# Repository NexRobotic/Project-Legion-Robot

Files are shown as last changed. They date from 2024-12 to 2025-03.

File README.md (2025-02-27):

# Project-Legion-Robot
 This is a 12 DOF Robot Based on RPI/Arduino/ESP32
    
This Repo Have Various Version of the Robot (Basicly All you need)

1. Arduino Without Servo Driver (This is the Simplest Version of Legion with Ardduino Nano And Nano Expansion Used Serial Monitor To Control)
2. Arduino With Servo Driver (This Version Use 16 Channel PCA Servo Driver WITH Arduino Solving pins issue, USE SDA and SCL)
3. Arduino With ESPCam  ("This Version Use Espcam and arduino to give live view and control interface, Use Rx Tx")
4. ESP32 (Since FlexiTimer2.h is not working on ESP Boards, i need to Find another way to Work on this Version any, 'IF ANY IDEA PLEASE CONTRIBUTE')
5. raspberri pi (This is The python Version, I am Using RPI 4 and Servo Driver for AI and ML Integration)

and Legion MARK 2 (this is the most advanced version of all)
watch the Youtube Video here 
Legion MARK 2 (https://www.youtube.com/watch?v=k1hns6NKTCY)

What to DO ?
1. 3d Print the Structure and Pick your Code Version
2. attach the servos to the structure (Use Servo Pin image for pin connection in media folder) (*without Servo horn)
3. Use Servo_Config Code to calibrate all the servo to 90
4. Attach all the servo horn maintaining the initial position (Use Initial position image in media folder) (*IMPORTANT)
5. Complete the Circuits and Upload/Run main code and enjoy



Note: 
Main Logic I used Was by Sunfounder Robot
panerqiang@sunfounder.com

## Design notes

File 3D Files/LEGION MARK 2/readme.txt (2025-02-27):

This is what you need to print 

legs with n20 holder X 2 (it have both left and right 1 so print this 2 pairs)
backward shoulder X 2
Forward Shoulder  X 2
femur             X 4
hinge             X 8
body top          X 1
body Bottom       X 1

USE tree support cuz its the best one

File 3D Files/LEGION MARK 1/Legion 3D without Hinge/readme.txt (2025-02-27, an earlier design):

This is what you need to print 

forward legs      X 2 
Backward legs     X 2 
backward shoulder X 2
Forward Shoulder  X 2
femur             X 4
body top          X 1
body Bottom       X 1

Note :
not using hinges will need fore filament as support and it will be slightly difficult to change the servo if needed

if you use hinges you need 16 screws (4 for each leg) to connect the hinges

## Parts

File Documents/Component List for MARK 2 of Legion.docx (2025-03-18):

# Component List for MARK 2 of Legion

Component | Quantity | Price per Unit (Rs) | Total Price (Rs)
MG99s 180 Degree Servo | 12 | 189 | 2268
Arduino Nano | 1 | 293 | 293
ESP32Cam with programmer | 1 | 1199 | 1199
UBEC SWITCH (5V 3AMP) | 1 | 496 | 496
L298N Motor driver | 1 | 284 | 284
N20 DC Geared Motor with wheels | 4 | 516 | 2064
18650 Rechargeable Cell | 3 | 295 | 885
18650 Rechargeable Cell Holder | 1 | 149 | 149
16 channel Servo driver | 1 | 540 | 540
Total Cost | | | 8178

Note: 3d part not included in the price

Additional Requirements

- On off Switch
- Jumper wires
- 3d printed parts and screws
- Antenna for esp32cam (optional)
- Ultrasonic sensor (optional)
- Faith (Compulsory)

Amazon link for legion basic chassis

https://www.amazon.in/Quadruped-Spider-Printed-Screws-without/dp/B08Z3SS53M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

Amazon Links For the component (Price or component may be Different use your BRAIN)

12 X MG99s 180 Degree Servo

: https://www.amazon.in/Digital-Gears-180°-Rotation-Airplanes-Helicopters-Pack/dp/B0CBMV1RGM/ref=sr_1_4?crid=DS6UM7TO7TCL&dib=eyJ2IjoiMSJ9.gsIwP0FZ_ynRjYAy3LY-lwEpQLO9WYkQDKRJBSf3uV9iHCB2bqO3dSaLnqgXOispJSwWp918hp2LtKmsguANecfjjdnFMcI5Km_-i6wgeWZ6gBxl5xIlLk11NyBa0-vFAfAS_Ow4o1VNdpOjxMRnWdQQo6zAgAlXlC13NaO-75OOEw7-qejtVtC9zuGgcaMpx8ZJG507RzabPAa1mW6YzjYGllxj_ESSCwc9TuIvjfAhrqjoOSVbeXBf6a6jlx9l2Aq7SJ4I94nEQSldhfr4_Ing01bRUSkesOmOi6u1H1BD0gS_1NldbJJWhSYbD2YMCyR43Fsn14fe1e9RW6LuXNimXdcUpq0Nf9_NtPuyXr4.0VStfd7wadzGoixJIKSlDUGHsjpPy6wrPN0ggZozOFg&dib_tag=se&keywords=mg99+servo&qid=1740650734&s=industrial&sprefix=mg99+servo%2Cindustrial%2C239&sr=1-4

1 X Arduino nano

: https://www.amazon.in/Robocraze-Improved-Version-Arduino-Soldered/dp/B077TJ8FCF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

1X ESP32Cam with programmer

: https://www.amazon.in/RoboThings-Camera-Module-Development-Bluetooth/dp/B098JQDKW3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

1 X Nano Expansion (you can also create a custom nano expansion PCB board)

https://www.amazon.in/Robocraze-Expansion-Adapter-Breakout-IO-Expansion/dp/B0941694M5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

1 X UBEC SWITCH (5V 3AMP)

https://www.amazon.in/Robocraze-Switch-Mode-Regulator-Multi-Rotor-Indicator/dp/B0DP54JVJY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

1 X L298N Motor driver

https://www.amazon.in/REES52-Controller-Module-Stepper-Arduino/dp/B072JWDK9B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

4 X N20 DC Geared Motor with wheels

https://www.amazon.in/Electron-Pack-Pcs-N20-3-7V/dp/B0CR8NHFWP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

3 X 18650 rechargeable cell
https://www.amazon.in/CONSONANTIAM-Capacity-Rechargeable-Batteries-Bluetooth/dp/B0DV5QTN5C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

1 X 18650 rechargeable cell holder

https://www.amazon.in/Electronic-Spices-Battery-Holder-Lithium/dp/B0B76KCLVF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

1X 16 channel Servo driver

https://www.amazon.in/TECHTONICS-PCA9685-16-Channel-12-Bit-Interface/dp/B09Y28RRH3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

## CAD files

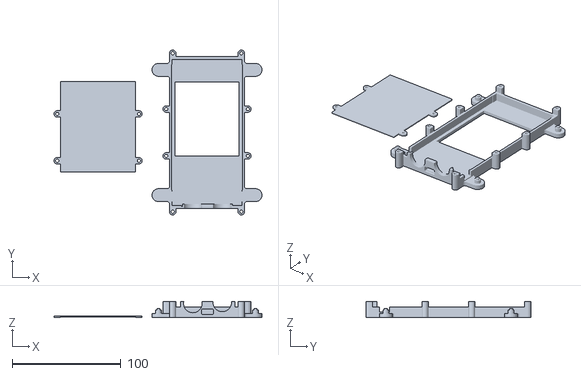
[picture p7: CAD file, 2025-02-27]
3D Files/LEGION MARK 2/body bottom.stl
191.0 x 151.5 x 15.0

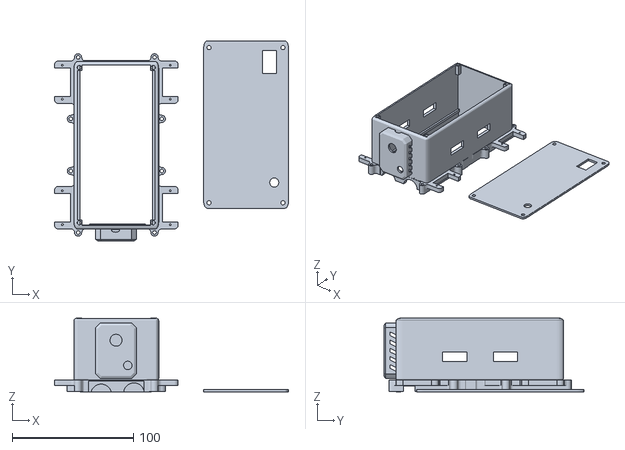
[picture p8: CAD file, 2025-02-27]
3D Files/LEGION MARK 2/body top.stl
193.0 x 165.0 x 61.0

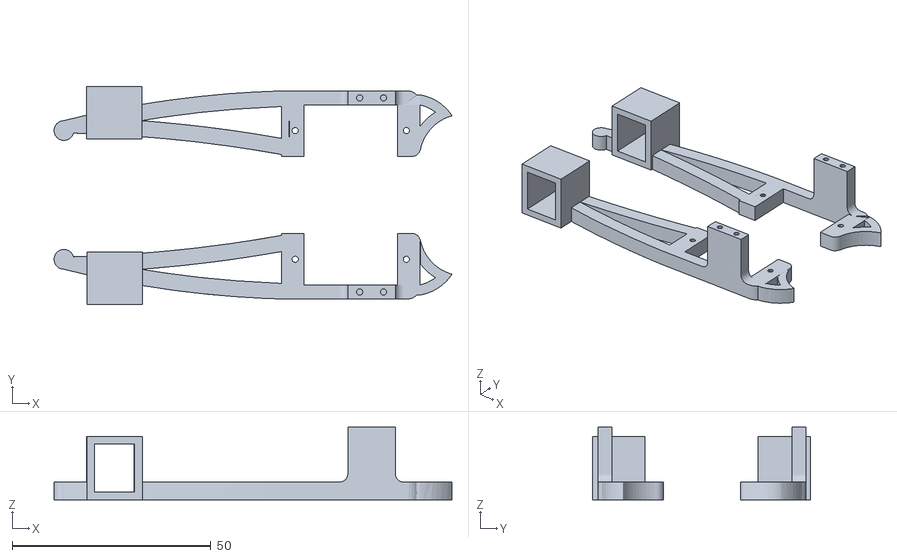
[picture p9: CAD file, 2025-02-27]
3D Files/LEGION MARK 2/legs with n20 holder.stl
100.2 x 54.9 x 18.3

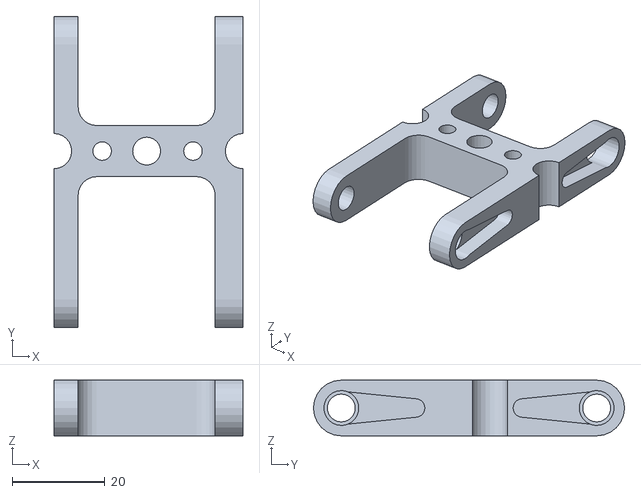
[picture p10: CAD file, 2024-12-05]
3D Files/LEGION MARK 2/femur.stl
40.7 x 67.0 x 12.0

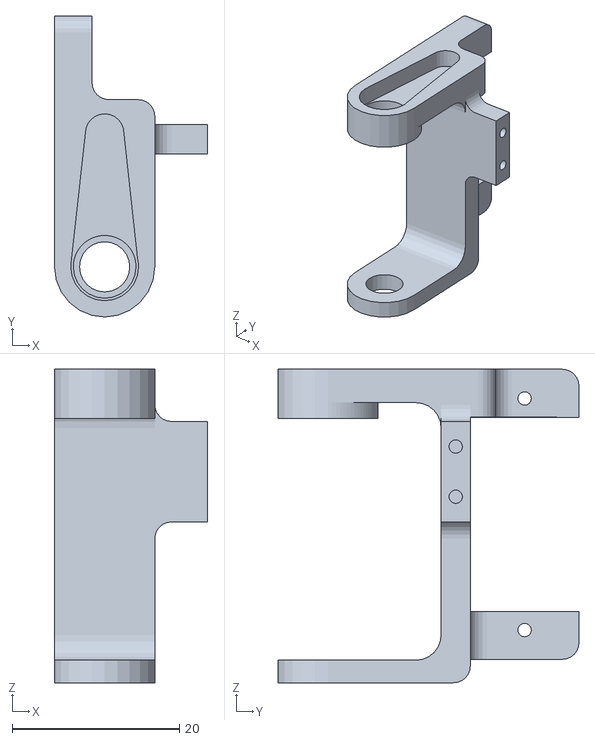
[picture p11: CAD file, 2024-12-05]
3D Files/LEGION MARK 2/backward shoulder.stl
18.3 x 36.0 x 37.5

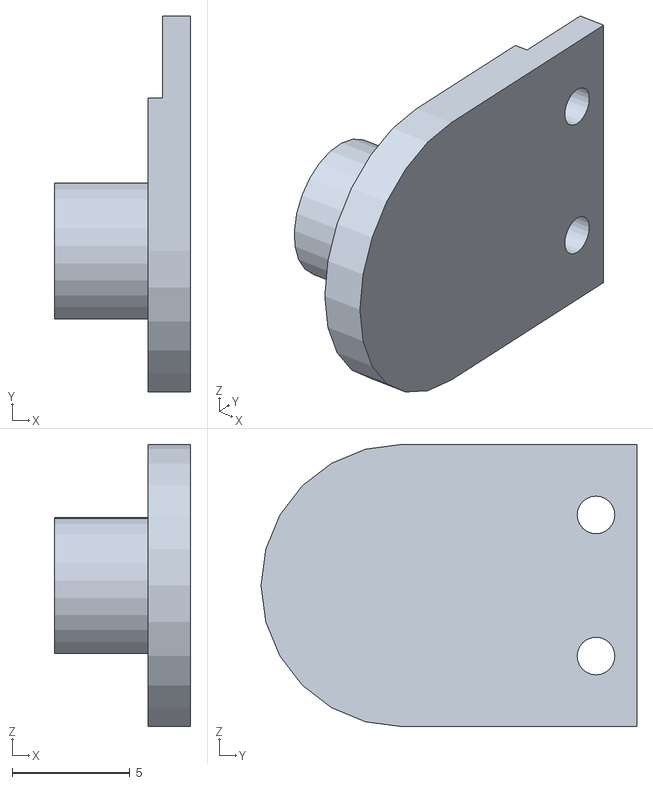
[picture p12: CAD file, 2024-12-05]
3D Files/LEGION MARK 2/hinge.stl
5.79 x 16.0 x 12.0

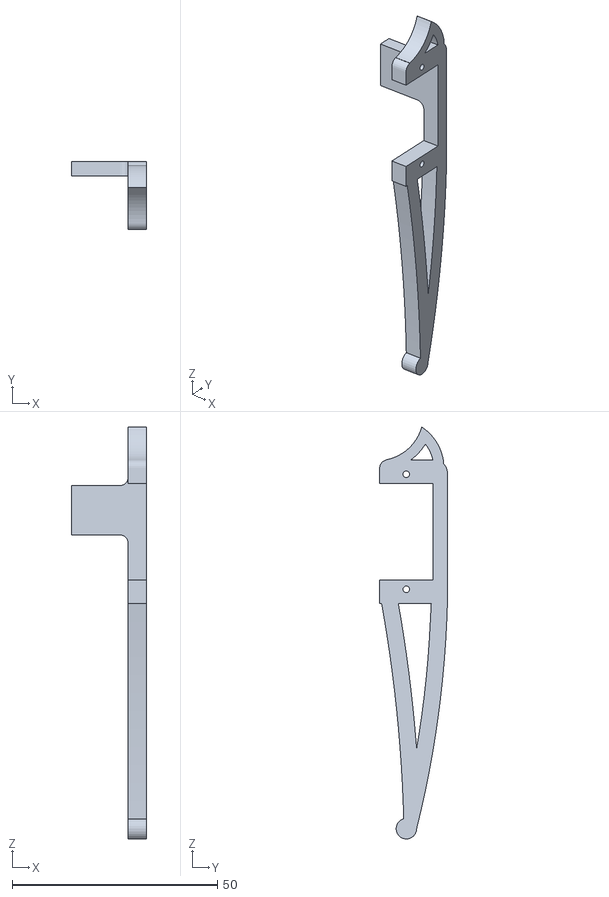
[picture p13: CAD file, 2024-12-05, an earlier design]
3D Files/LEGION MARK 1/Legion 3D with hinge/files/backward legs.stl
18.3 x 16.5 x 100.2

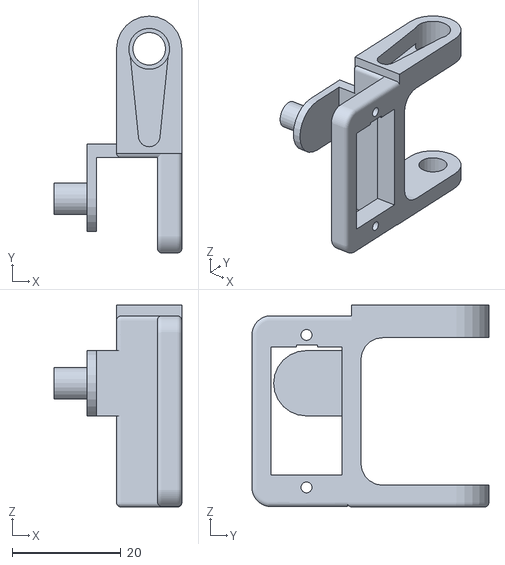
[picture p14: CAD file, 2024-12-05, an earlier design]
3D Files/LEGION MARK 1/Legion 3D without Hinge/files/forward Shoulders.stl
23.5 x 43.5 x 37.1

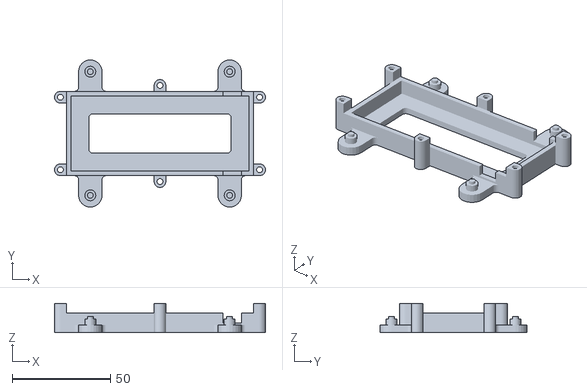
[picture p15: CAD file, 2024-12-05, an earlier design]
3D Files/LEGION MARK 1/Legion 3D with hinge/files/body_bottom.stl
107.5 x 75.0 x 15.0

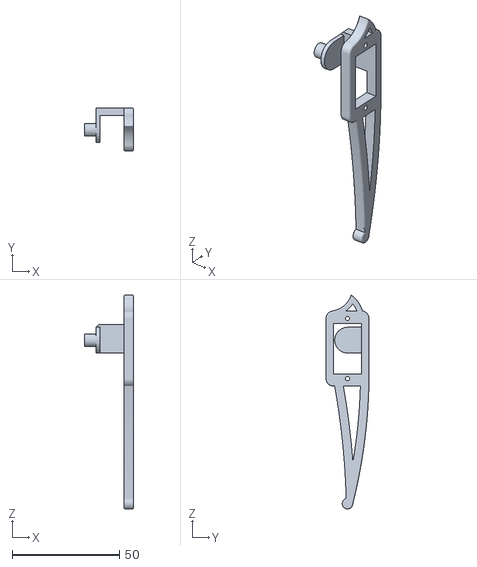
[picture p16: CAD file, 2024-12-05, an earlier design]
3D Files/LEGION MARK 1/Legion 3D without Hinge/files/forward leg.stl
23.0 x 20.0 x 99.7

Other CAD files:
3D Files/LEGION MARK 2/forward shoulder.stl
3D Files/LEGION MARK 1/Legion 3D with hinge/files/forward shoulder.stl
3D Files/LEGION MARK 1/Legion 3D with hinge/files/forward legs.stl
3D Files/LEGION MARK 1/Legion 3D without Hinge/files/backward Shoulders.stl
3D Files/LEGION MARK 1/Legion 3D with hinge/files/body_top.stl
3D Files/LEGION MARK 1/Legion 3D without Hinge/files/backward legs.stl
3D Files/LEGION MARK 1/Legion 3D without Hinge/files/body_top.stl

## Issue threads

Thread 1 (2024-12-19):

List of parts

Skwarson96, 2024-12-19:
Hello
Can you add a detailed list of parts to print? You can guess what is needed but it would be easier with a specific list

NexRobotic, 2024-12-30:
Leg-f x 2
Leg-b x 2
Shoulder-f x 2
Shoulder-b x 2
femur x 4
hinge x 8
body-top x 1
body-bottom x 1

Closed 2025-01-04.

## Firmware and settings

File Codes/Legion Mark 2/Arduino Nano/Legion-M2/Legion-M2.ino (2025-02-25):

//Mark 2 : Wheel on legion go Round and Round


#include <Servo.h>
#include <FlexiTimer2.h>
#include "Legion_config.h"
#include "Legion.h"
#include <Adafruit_PWMServoDriver.h>

// Create a PCA9685 object
Adafruit_PWMServoDriver pwm = Adafruit_PWMServoDriver();

// Servo configuration
#define SERVOMIN 150  // Minimum pulse length count
#define SERVOMAX 600  // Maximum pulse length count

//DIctionary
#define FORWARD 'f'
#define BACKWARD 'b'
#define LEFT 'l'
#define RIGHT 'r'
#define STOP's'
#define SIT 'i'

#define HEIGHTUP 'u'
#define HEIGHTDOWN'v'

#define MOVEFORWARD 'w'
#define MOVEBACKWARD 'x'
#define MOVELEFT 'a'
#define MOVERIGHT 'd'


#define HANDWAVE 'e'
#define HANDSHAKE 'g'

 #define DRIVEMODE 'h'
// #define  'j'
// #define  'k'
// #define  'm'
// #define  'n'
// #define  'o'
// #define  'p'
// #define  'q'
// #define  't'
// #define  'Y'
// #define  'z'

//DIctionary


void RC_Control();

const int channelPins[] = { A1, A2, A3, A4, A5, A6 };
const int numChannels = 6;

unsigned long pulseWidths[numChannels];
int channelValues[numChannels];


// Threshold values for mizn and max pulse widths
const int minValue = 1000;
const int maxValue = 1800;
unsigned long TIME_INTERVAL = 35000;  // Timeout in microseconds (adjust based on your RC receiver)

Legion legion;

bool state = true;
char cmd = STOP;
bool check_service = false;

/* Servos --------------------------------------------------------------------*/
//define 12 servos for 4 legs

void setup() {
  Serial.begin(115200);
  Serial.println("Robot starts initialization");
  pwm.begin();
  pwm.setPWMFreq(60);  // Set frequency to 50 Hz for servos
  delay(10);

  pinMode(motorPinA1, OUTPUT);
  pinMode(motorPinA2, OUTPUT);
  pinMode(motorPinB1, OUTPUT);
  pinMode(motorPinB2, OUTPUT);
  pinMode(enA, OUTPUT);
  pinMode(enB, OUTPUT);


  analogWrite(enA, 60);
  analogWrite(enB, 50);



  // for (int i = 0; i < numChannels; i++) {
  //   pinMode(channelPins[i], INPUT);
  // }
  //initialize default parameter
  
  legion.set_site(0, x_default - x_offset, y_start + y_step, z_boot);
  legion.set_site(1, x_default - x_offset, y_start + y_step, z_boot);
  legion.set_site(2, x_default + x_offset, y_start, z_boot);
  legion.set_site(3, x_default + x_offset, y_start, z_boot);
  for (int i = 0; i < 4; i++) {
    for (int j = 0; j < 3; j++) {
      site_now[i][j] = site_expect[i][j];
    }
  }
  //start servo service
  FlexiTimer2::set(20, servo_service);
  FlexiTimer2::start();
  Serial.println("Servo service started");
  Serial.println("Servos initialized");
  Serial.println("Robot initialization Complete");
  
  legion.stand();
  //legion.climb();
}

int angleToPWM(float angle) {
  return map(angle, 0, 180, SERVOMIN, SERVOMAX);
}

// Set servo angles using PCA9685
void setServoAngle(int channel, float angle) {
  int pwmValue = angleToPWM(angle);
  pwm.setPWM(channel, 0, pwmValue);
}


void loop() {
  // RC_Control();
  // servicetest();
  gaits(cmd);
  //legion.climb();

}

// void serialEvent() {
//   char tmp = -1;
//   boolean taken = false;  // is steps already taken?

//   while (Serial.available()) {
//     state = !state;       // inverse state
//     tmp = Serial.read();  //Serial.println(cmd);
//     taken = gaits(tmp);   // steps taken?

//     if (taken)  // basically repeat the previous serial command
//       cmd = tmp;
//   }
// }

void serialEvent() {

  String command = "";
  while (Serial.available()) {
    state = !state;  // inverse state
    char c = (char)Serial.read();
    if (c == '\n') {  // End of command
      break;
    }
    command += c;
  }
  command.trim();  // Remove extra whitespace or newlines
  Serial.println(command);
  // Handle movement commands
  if (command == "f") cmd = FORWARD;
  else if (command == "b") cmd = BACKWARD;
  else if (command == "l") cmd = LEFT;
  else if (command == "r") cmd = RIGHT;
  else if (command == "s") cmd = STOP;
  else if (command == "w") cmd = MOVEFORWARD;
  else if (command == "x") cmd = MOVEBACKWARD;
  else if (command == "a") cmd = MOVELEFT;
  else if (command == "d") cmd = MOVERIGHT;
  else if (command == "h") cmd = DRIVEMODE;
  else if (command == "u"){
    legion.adjustheight(true);
  }
  else if (command == "v"){
    legion.adjustheight(false);
  }


  else if (command.startsWith("xd,")) {
    int value = command.substring(3).toInt();  // Extract value
    //Serial.println(command);
    legion.adjust('x', value);
  } else if (command.startsWith("yd,")) {
    int value = command.substring(3).toInt();  // Extract value
    legion.adjust('y', value);
    //Serial.println(command);
  } else if (command.startsWith("zd,")) {
    int value = command.substring(3).toInt();  // Extract value
    legion.adjust('z', value);
    //Serial.println(command);
  } else if (command.startsWith("ls,")) {
    int value = command.substring(3).toInt();  // Extract value
    legion.adjust('l', value);
    //Serial.println(command);
  } else if (command.startsWith("ss,")) {
    int value = command.substring(3).toInt();  // Extract value
    analogWrite(enA, value);
    analogWrite(enB, value);
    // legion.adjust("ss", value);
    //Serial.println(command);
  }
}

// void serialEvent() {
//   while (Serial.available()) {
//     char tmp = -1;
//     boolean taken = false;  // is steps already taken?
//     state = !state;       // inverse state
//     tmp = Serial.read();  //Serial.println(cmd);
//     taken = gaits(tmp);   // steps taken?

//     if (taken)  // basically repeat the previous serial command
//       cmd = tmp;
//   }
// }


// Function to process received serial commands

boolean gaits(char cmd) {
  bool taken = true;
  switch (cmd) {
    case FORWARD:
      legion.step_forward(1);
      break;
    case BACKWARD:
      legion.step_back(1);
      break;
    case RIGHT:
      legion.turn_right(1);
      break;
    case LEFT:
      legion.turn_left(1);
      break;
    case STOP:
      legion.stand();
      legion.MS();
      break;
    case SIT:
      legion.sit();
      break;
    case MOVEFORWARD:
      legion.MF();
      break;
    case MOVEBACKWARD:
      legion.MB();
      break;
    case MOVELEFT:
      legion.ML();
      break;
    case MOVERIGHT:
      legion.MR();
      break;
    case HANDWAVE:
      legion.hand_wave(3);
      break;
    case HANDSHAKE:
      legion.hand_shake(3);
      break;
    case HEIGHTUP:
      legion.adjustheight(true);
      //cmd=STOP;
      taken = false;
      break;
    case HEIGHTDOWN:
      legion.adjustheight(false);
      //cmd=STOP;
      taken = false;
      break;
    case DRIVEMODE:
      legion.drivemode();
      //cmd=STOP;
      taken = false;
      break;
    // case HEADUP:
    //   legion.head_up(3);
    //   break;
    // case HEADDOWN:
    //   legion.head_down(3);
    //   break;
    // case BODYRIGHT:
    //   legion.body_right(15);
    //   break;
    // case BODYLEFT:
    //   legion.body_left(15);
    //   break;
    // case DANCE:
    //   legion.body_dance(5);
    //   break;

    default:
      taken = false;
  }
  return taken;
}



/*
  - microservos service /timer interrupt function/50Hz
  - when set site expected,this function move the end point to it in a straight line
  - temp_speed[4][3] should be set before set expect site,it make sure the end point
   move in a straight line,and decide move speed.
   ---------------------------------------------------------------------------*/
void servo_service(void) {
  sei();
  static float alpha, beta, gamma;

  for (int i = 0; i < 4; i++) {
    for (int j = 0; j < 3; j++) {
      if (abs(site_now[i][j] - site_expect[i][j]) >= abs(temp_speed[i][j]))
        site_now[i][j] += temp_speed[i][j];
      else
        site_now[i][j] = site_expect[i][j];
    }

    cartesian_to_polar(alpha, beta, gamma, site_now[i][0], site_now[i][1], site_now[i][2]);
    polar_to_servo(i, alpha, beta, gamma);
  }

  rest_counter++;
}


void cartesian_to_polar(volatile float &alpha, volatile float &beta, volatile float &gamma, volatile float x, volatile float y, volatile float z) {
  //calculate w-z degree
  float v, w;
  w = (x >= 0 ? 1 : -1) * (sqrt(pow(x, 2) + pow(y, 2)));
  v = w - length_c;
  alpha = atan2(z, v) + acos((pow(length_a, 2) - pow(length_b, 2) + pow(v, 2) + pow(z, 2)) / 2 / length_a / sqrt(pow(v, 2) + pow(z, 2)));
  beta = acos((pow(length_a, 2) + pow(length_b, 2) - pow(v, 2) - pow(z, 2)) / 2 / length_a / length_b);
  //calculate x-y-z degree
  gamma = (w >= 0) ? atan2(y, x) : atan2(-y, -x);
  //trans degree pi->180
  alpha = alpha / pi * 180;
  beta = beta / pi * 180;
  gamma = gamma / pi * 180;
}

/*
  - trans site from polar to microservos
  - mathematical model map to fact
  - the errors saved in eeprom will be add
   ---------------------------------------------------------------------------*/
void polar_to_servo(int leg, float alpha, float beta, float gamma) {
  if (leg == 0) {
    alpha = 90 - alpha;
    beta = beta;
    gamma += 90;
  } else if (leg == 1) {
    alpha += 90;
    beta = 180 - beta;
    gamma = 90 - gamma;
  } else if (leg == 2) {
    alpha += 90;
    beta = 180 - beta;
    gamma = 90 - gamma;
  } else if (leg == 3) {
    alpha = 90 - alpha;
    beta = beta;
    gamma += 90;
  }

  setServoAngle(servo_channels[leg][0], alpha);
  setServoAngle(servo_channels[leg][1], beta);
  setServoAngle(servo_channels[leg][2], gamma);
}

void RC_Control() {
  pulseWidths[0] = pulseIn(channelPins[0], HIGH, TIME_INTERVAL);
  pulseWidths[1] = pulseIn(channelPins[1], HIGH, TIME_INTERVAL);
  pulseWidths[2] = pulseIn(channelPins[2], HIGH, TIME_INTERVAL);
  pulseWidths[3] = pulseIn(channelPins[3], HIGH, TIME_INTERVAL);
  pulseWidths[4] = pulseIn(channelPins[4], HIGH, TIME_INTERVAL);
  // pulseWidths[5] = pulseIn(channelPins[5], HIGH, TIME_INTERVAL);

  // Serial.println(pulseWidths[0]);
  // Serial.println(pulseWidths[1]);

  channelValues[0] = (pulseWidths[0] > 1500) ? 1 : (pulseWidths[0] < 1100) ? -1
                                                                           : 0;
  channelValues[1] = (pulseWidths[1] > 1500) ? 1 : (pulseWidths[1] < 1100) ? -1
                                                                           : 0;
  // channelValues[2] = (pulseWidths[2] > 1500) ? 1 : (pulseWidths[2] < 1100) ? -1 : 0;
  // channelValues[3] = (pulseWidths[3] > 1500) ? 1 : (pulseWidths[3] < 1100) ? -1 : 0;
  // channelValues[4] = (pulseWidths[4] > 1500) ? 1 : (pulseWidths[4] < 1100) ? -1: 0;
  // channelValues[5] = (pulseWidths[5] > 1500) ? 1 : (pulseWidths[5] < 1100) ? -1 : 0;

  // // Initialize tmp2 to STAND by default
  boolean taken2 = false;  // is steps already taken?
  char tmp2 = -1;

  // // Determine command based on channel values
  if (channelValues[0] != 0) {
    if (channelValues[0] == -1) {
      tmp2 = LEFT;
    } else if (channelValues[0] == 1) {
      tmp2 = RIGHT;
    }
  } else if (channelValues[1] != 0) {
    if (channelValues[1] == -1) {
      tmp2 = BACKWARD;
    } else if (channelValues[1] == 1) {
      tmp2 = FORWARD;
    }
  } else {
    tmp2 = STOP;  // Default to STAND if no valid channel values
  }

  // heightValue = map(pulseWidths[2], 1000, 2000, 0, 100);  // Assuming 1000 to 2000 as pulse width range
  // heightValue = constrain(heightValue, 0, 100);  // Ensure the value stays within 0-100

  int Speed = map(pulseWidths[4], 1000, 2000, 300, 1500);  // Assuming 1000 to 2000 as pulse width range
  Speed = constrain(Speed, 300, 1500);                     // Ensure the value stays within 0-100  // Call adjustHeight with mapped value

  taken2 = gaits(tmp2);
  // // Update command and execute gait if changed

  if (taken2) {
    cmd = tmp2;  // Update cmd if the command was valid
  }
  delay(100);
}

void servicetest() {
  Serial.println("Stand");
  legion.stand();
  delay(2000);
  Serial.println("Step forward");
  legion.step_forward(3);
  delay(2000);
  Serial.println("Step back");
  legion.step_back(3);
  delay(2000);
  Serial.println("Turn left");
  legion.turn_left(3);
  delay(2000);
  Serial.println("Turn right");
  legion.turn_right(3);
  delay(2000);
  legion.hand_shake(3);
  delay(2000);
  legion.hand_wave(3);
  delay(2000);
  // legion.body_dance(3);
  // delay(2000);
  legion.sit();
  delay(2000);
  legion.stand();
  delay(2000);
  legion.head_up(20);
  delay(1000);
  legion.step_forward(3);
  delay(1000);
  legion.head_down(20);
  delay(1000);
  legion.head_down(20);
  delay(2000);
  legion.step_back(3);
  delay(2000);
  legion.sit();
  delay(2000);
  check_service = true;
}

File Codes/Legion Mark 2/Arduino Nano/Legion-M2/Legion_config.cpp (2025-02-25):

#include "Legion_config.h"
#include <math.h> 
#include <Arduino.h>

// Servo settings
Servo servo[4][3];
const int servo_channels[4][3] = { {0, 1, 2}, {4, 5, 6}, {8, 9, 10}, {12, 13, 14} };

// Robot size constants original
// const float length_a = 55;
// const float length_b = 77.5;
// const float length_c = 27.5;
// const float length_side = 71;
// const float z_absolute = -28;

// Robot size constants original M2
const float length_a = 55;
const float length_b = 77.5;
const float length_c = 27.5;
const float length_side = 113;
const float z_absolute = -28;
// Movement constants

float z_default = -60, z_up = -30, z_boot = z_absolute; //-60=z_default
float x_default = 70, x_offset = 0;
float y_start = 0, y_step = 40;
float y_default = 62;
float spot_turn_speed = 4;
float leg_move_speed = 8;
float body_move_speed = 3;
float stand_seat_speed = 1;
float KEEP = 255;
float pi = 3.1415926;

// Turn constants
const float temp_a = sqrt(pow(2 * x_default + length_side, 2) + pow(y_step, 2));
const float temp_b = 2 * (y_start + y_step) + length_side;
const float temp_c = sqrt(pow(2 * x_default + length_side, 2) + pow(2 * y_start + y_step + length_side, 2));
const float temp_alpha = acos((pow(temp_a, 2) + pow(temp_b, 2) - pow(temp_c, 2)) / 2 / temp_a / temp_b);
const float turn_x1 = (temp_a - length_side) / 2;
const float turn_y1 = y_start + y_step / 2;
const float turn_x0 = turn_x1 - temp_b * cos(temp_alpha);
const float turn_y0 = temp_b * sin(temp_alpha) - turn_y1 - length_side;

// Variables for movement
volatile float site_now[4][3];
volatile float site_expect[4][3];
float temp_speed[4][3];
float move_speed;
float speed_multiple = 1;
volatile int rest_counter;

const int motorPinA1 = 2;
const int motorPinA2 = 3;
const int motorPinB1 = 4;
const int motorPinB2 = 5;
const int enA = 6;
const int enB = 9;

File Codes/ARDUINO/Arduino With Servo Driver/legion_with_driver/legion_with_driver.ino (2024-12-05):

/*
NANO Connections
VCC - 3.7v
SDA - A4
SCL - A5
GND - GND
*/

#include <Servo.h>    //to define and control servos
#include <FlexiTimer2.h>//to set a timer to manage all servos
#include <Wire.h>
#include <Adafruit_PWMServoDriver.h>

// Create a PCA9685 object
Adafruit_PWMServoDriver pwm = Adafruit_PWMServoDriver();

// Servo configuration
#define SERVOMIN  150 // Minimum pulse length count
#define SERVOMAX  600 // Maximum pulse length count
/* Servos --------------------------------------------------------------------*/
//define 12 servos for 4 legs
Servo servo[4][3];
//define servos' ports
const int servo_channels[4][3] = { {0, 1, 2}, {4, 5, 6}, {8, 9, 10}, {12, 13, 14} };
/* Size of the robot ---------------------------------------------- -----------*/
const float length_a = 55;
const float length_b = 77.5;
const float length_c = 27.5;
const float length_side = 71;
const float z_absolute = -28;
/* Constants for movement ----------------------------------------------------*/
const float z_default = -50, z_up = -30, z_boot = z_absolute;
const float x_default = 62, x_offset = 0;
const float y_start = 0, y_step = 40;
const float y_default = x_default;
/* variables for movement ----------------------------------------------------*/
volatile float site_now[4][3];    //real-time coordinates of the end of each leg
volatile float site_expect[4][3]; //expected coordinates of the end of each leg
float temp_speed[4][3];   //each axis' speed, needs to be recalculated before each movement
float move_speed;     //movement speed
float speed_multiple = 1; //movement speed multiple
const float spot_turn_speed = 4;
const float leg_move_speed = 8;
const float body_move_speed = 3;
const float stand_seat_speed = 1;
volatile int rest_counter;      //+1/0.02s, for automatic rest
//functions' parameter
const float KEEP = 255;
//define PI for calculation
const float pi = 3.1415926;
/* Constants for turn --------------------------------------------------------*/
//temp length
const float temp_a = sqrt(pow(2 * x_default + length_side, 2) + pow(y_step, 2));
const float temp_b = 2 * (y_start + y_step) + length_side;
const float temp_c = sqrt(pow(2 * x_default + length_side, 2) + pow(2 * y_start + y_step + length_side, 2));
const float temp_alpha = acos((pow(temp_a, 2) + pow(temp_b, 2) - pow(temp_c, 2)) / 2 / temp_a / temp_b);
//site for turn
const float turn_x1 = (temp_a - length_side) / 2;
const float turn_y1 = y_start + y_step / 2;
const float turn_x0 = turn_x1 - temp_b * cos(temp_alpha);
const float turn_y0 = temp_b * sin(temp_alpha) - turn_y1 - length_side;
/* ---------------------------------------------------------------------------*/

/*
  - setup function
   ---------------------------------------------------------------------------*/
void setup()
{
  //start serial for debug
  Serial.begin(115200);
    Serial.println("ESP32 Robot Initialization");

    // Initialize PCA9685
    pwm.begin();
    pwm.setPWMFreq(60); // Set frequency to 50 Hz for servos
    delay(10);
  //initialize default parameter
  set_site(0, x_default - x_offset, y_start + y_step, z_boot);
  set_site(1, x_default - x_offset, y_start + y_step, z_boot);
  set_site(2, x_default + x_offset, y_start, z_boot);
  set_site(3, x_default + x_offset, y_start, z_boot);
  for (int i = 0; i < 4; i++)
  {
    for (int j = 0; j < 3; j++)
    {
      site_now[i][j] = site_expect[i][j];
    }
  }
  //start servo service
  FlexiTimer2::set(20, servo_service);
  FlexiTimer2::start();
  Serial.println("Servo service started");
  //initialize servos
  //servo_attach();
  Serial.println("Servos initialized");
  Serial.println("Robot initialization Complete");
}

int angleToPWM(float angle) {
    return map(angle, 0, 180, SERVOMIN, SERVOMAX);
}

// Set servo angles using PCA9685
void setServoAngle(int channel, float angle) {
    int pwmValue = angleToPWM(angle);
    pwm.setPWM(channel, 0, pwmValue);
}

// void servo_attach(void)
// {
//   for (int i = 0; i < 4; i++)
//   {
//     for (int j = 0; j < 3; j++)
//     {
//       servo[i][j].attach(servo_pin[i][j]);
//       delay(100);
//     }
//   }
// }

// void servo_detach(void)
// {
//   for (int i = 0; i < 4; i++)
//   {
//     for (int j = 0; j < 3; j++)
//     {
//       servo[i][j].detach();
//       delay(100);
//     }
//   }
// }
/*
  - loop function
   ---------------------------------------------------------------------------*/
void loop()
{
  Serial.println("Stand");
  stand();
  delay(2000);
  Serial.println("Step forward");
  step_forward(5);
  delay(2000);
  Serial.println("Step back");
  step_back(5);
  delay(2000);
  Serial.println("Turn left");
  turn_left(5);
  delay(2000);
  Serial.println("Turn right");
  turn_right(5);
  delay(2000);
  Serial.println("Hand wave");
  hand_wave(3);
  delay(2000);
  Serial.println("Hand wave");
  hand_shake(3);
  delay(2000);  
  Serial.println("Body dance");
  body_dance(10);
  delay(2000);    
  Serial.println("Sit");
  sit();
  delay(5000);
}

/*
  - sit
  - blocking function
   ---------------------------------------------------------------------------*/
void sit(void)
{
  move_speed = stand_seat_speed;
  for (int leg = 0; leg < 4; leg++)
  {
    set_site(leg, KEEP, KEEP, z_boot);
  }
  wait_all_reach();
}

/*
  - stand
  - blocking function
   ---------------------------------------------------------------------------*/
void stand(void)
{
  move_speed = stand_seat_speed;
  for (int leg = 0; leg < 4; leg++)
  {
    set_site(leg, KEEP, KEEP, z_default);
  }
  wait_all_reach();
}
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

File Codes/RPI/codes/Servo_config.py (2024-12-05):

from adafruit_pca9685 import PCA9685
from board import SCL, SDA
import busio
import time

# Initialize I2C and PCA9685
i2c = busio.I2C(SCL, SDA)
pca = PCA9685(i2c)
pca.frequency = 60  # Set frequency to 50Hz for servos

# Servo channels for the 12 servos
servo_channels = list(range(15))  # Channels 0-16

# Define servo limits
SERVOMIN = 150  # Minimum pulse length count (from Arduino code)
SERVOMAX = 600  # Maximum pulse length count (from Arduino code)

# Helper function to set servo angle
def set_servo_angle(channel, angle):
    """
    Set a servo to a specific angle (0-180 degrees).
    :param channel: PCA9685 channel (0-11)
    :param angle: Desired angle (0-180 degrees)
    """
    pulse = int(SERVOMIN + (angle / 180.0) * (SERVOMAX - SERVOMIN))
    duty_cycle = int((pulse / 4096.0) * 65536)  # Convert to 16-bit duty cycle
    pca.channels[channel].duty_cycle = duty_cycle

# Main program to move all 12 servos to 90 degrees
try:
    print("Setting all servos to 90 degrees...")
    for channel in servo_channels:
        set_servo_angle(channel, 90)  # Set to 90 degrees
        time.sleep(0.1)  # Small delay to allow servo movement

    print("All servos are set to 90 degrees.")
    time.sleep(5)  # Keep the servos in position for 5 seconds
finally:
    # Deinitialize PCA9685 to free up resources
    pca.deinit()
    print("Program finished.")

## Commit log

2024-12-05 project init
    [backward Shoulders.stl, backward legs.stl, backward shoulder.stl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]
2025-02-27 update mark2 3d files and budget report
    [backward Shoulders.stl, backward legs.stl, backward shoulder.stl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]
2025-02-28 adding circuit diagram
    [legion Mark 2 Circuit Diagram.fzz]
